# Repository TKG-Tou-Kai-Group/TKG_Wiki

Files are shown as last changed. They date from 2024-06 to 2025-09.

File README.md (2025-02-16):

# TKG Wiki

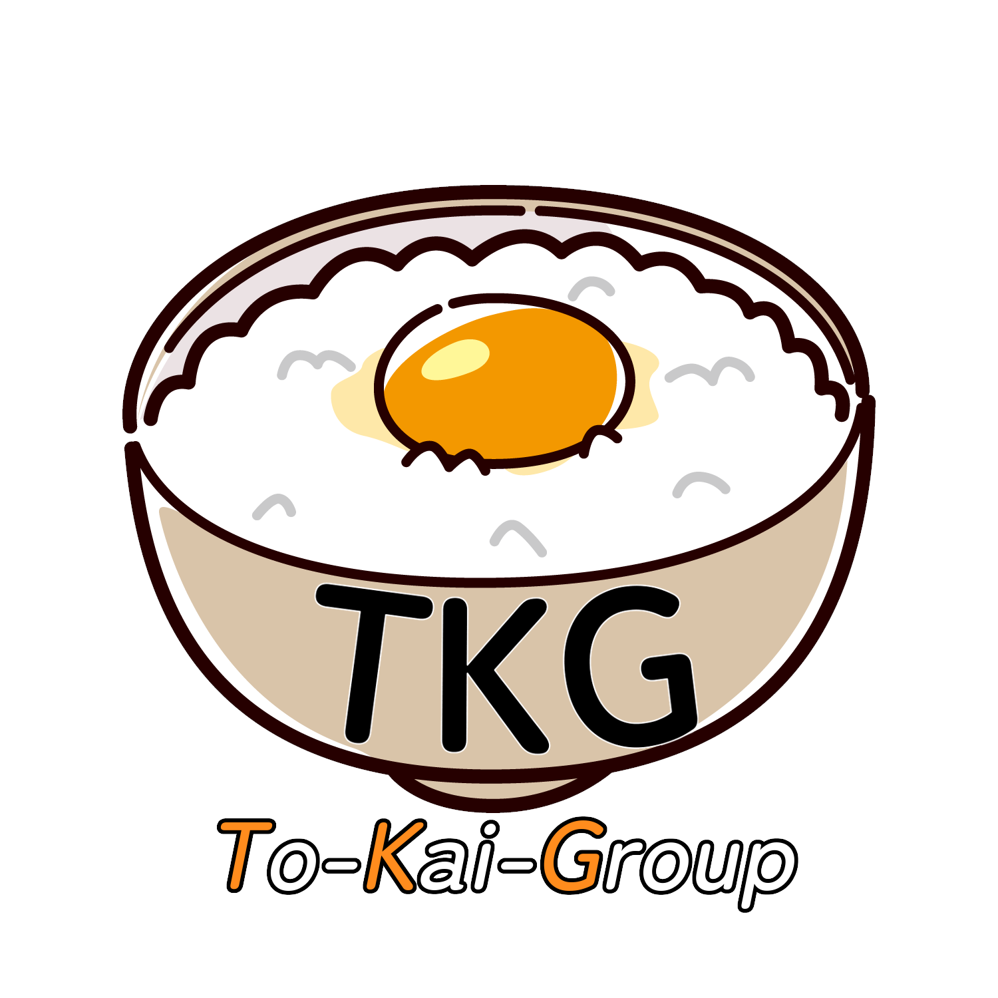
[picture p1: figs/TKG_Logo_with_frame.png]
ロゴ


## TKGについて

[CoRE](https://core.scramble-robot.org/)というエンジニア選手権に出場するために結成された東海地方4社の社会人連合チームです。メンバーにはお酒好きが多く、お酒がエネルギー源です。前回大会の目標は「技術賞・個人賞の受賞」でした。革新的技術賞を受賞できましたが、各構成要素の信頼性が低く同盟戦では活躍できませんでした。2024年度は「各構成要素の信頼性向上」により同盟戦で活躍できるロボットを開発することで、総合優勝を目指します！x（旧Twitter）上の#CoREJP_TKGで進捗状況や技術資料を公開中です。微力ながら大会を盛り上げていきますので、どうぞよろしくお願いします。

## 本Wikiの内容について

各出場年毎に作成した設計検討資料をアップロードしています。内容として、ウォーターフォール型開発モデルに基づく方針決定、外部設計、詳細設計の検討資料に加えて、作成したロボットの3DCADデータや回路基板データがあります。詳しい情報は各年毎のREADMEを参照してください。

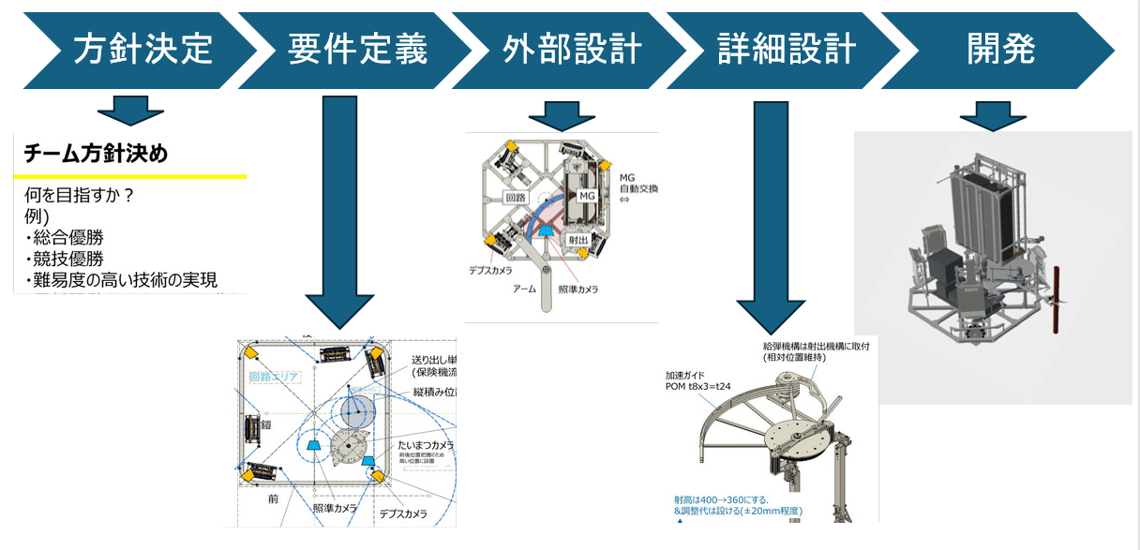
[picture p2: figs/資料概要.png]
資料概要


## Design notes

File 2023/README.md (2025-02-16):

# TKG - CoRE 2023 資料

CoRE 2023に出場した際に作成した企画・構想段階の資料や機能ブロック図などが格納されています。

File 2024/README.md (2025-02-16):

# TKG - CoRE 2024 資料

CoRE 2024に出場した際に作成した資料です。以下の4つのフォルダからなります。

- [本命マシン_開発資料](./本命マシン_開発資料)

  新規開発の機能を盛り込んだ機体の開発時に作成した方針決定、構想DR、外部仕様DR、詳細設計レビューやスケジュールの資料が格納されています。

- [保険マシン_開発資料](./保険マシン_開発資料/)

  昨年開発したマシンを元に確実に動作することを目標としたバックアップ用機体の構想設計、詳細設計の資料が格納されています。

- [02_詳細検討](./02_詳細検討/)

  具体的に設計したロボットの3DCADや基板データ、計算書などが格納されています。
  3DCADデータとして、比較的利用が容易なFusion 360用のアーカイブファイルと様々な3DCADで開くことができるSTEPファイルをZIP圧縮したものを用意しています。

- [提出済書類](./提出済書類/)

  大会運営に提出した審査資料が格納されています。大会運営が公開する以前から他のチームの参考として公開しているものとなります。
  大会運営から公開されている全チームの資料は[こちら](https://drive.google.com/drive/folders/1EVPRaTSho4vyFh4uzZCRXxRpLFyxL3u6)です。

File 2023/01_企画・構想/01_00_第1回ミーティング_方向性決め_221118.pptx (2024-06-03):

## 第1回 チームMTG

□方向性決め
□日程確認

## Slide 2

チームの目標設定

何を目指すか
例えば，
・総合優勝
・競技優勝
・難易度の高い技術の実装(勝敗を問わない)
・最低限動くものをみんなで作り上げること
・学生が絶対にできないことをやる(勝敗を問わない)
・社会人らしさを
設定した各目標に対して、それを実現するロボットはどんなものか考える．

最低限動くもの(一通りの競技ができる)を本年度の目標とする
回を重ねるごとに付加価値をつけていく(同じルールは3年間)

チーム目標

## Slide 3

日程

タイトです．

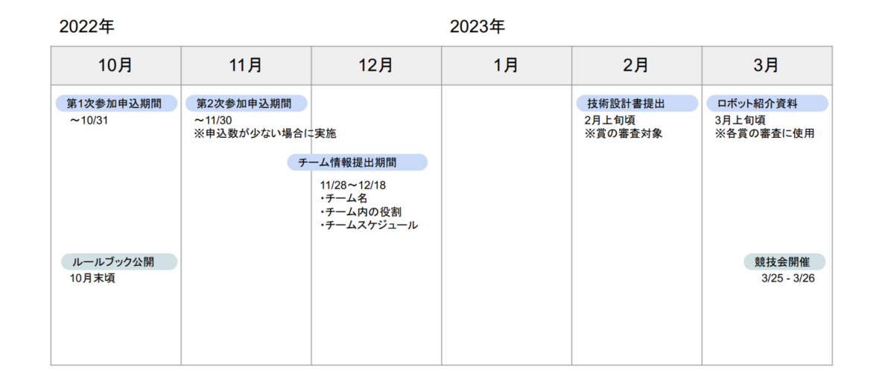
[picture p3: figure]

アイデア出し
方針決定
計画立案

構想
要件定義

12/M

現実的な予定

詳細検討

製造・手配

組立

検証・調整

1/M

2/M

理想的な予定

詳細検討

製造/組立/手配

正月休み明けから
製造に入るイメージ

検証・調整

脚周りは先行して製作・動作確認

独立要素の先行詳細検討
(足周りとか)

先行手配

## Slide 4

方向性決め

汎用型
└1台で一通りの競技をこなせる
└移動機能:対向2輪，オムニ3輪，オムニ4輪，メカナム(4輪)，独立4輪ステア
└投射機能:ローラー，ベルト，ばね・ゴム
└装填機能
└旗回収/設置機能
└たいまつ設置機能
汎用型+付加価値
操縦者補助
└
回転砲塔
転倒復帰

特化型
└例)固定砲台:攻撃に全振り

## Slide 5

最低限のアイデア

・対向2輪
・投射機構1発:ベルト式 or ローラー式
・仰角調整機構有り
・装填機構:自重落下
・操作画面はデフォルト
・旗/たいまつ回収/設置機構：つかむ+上下動(アクチュエータ2個)

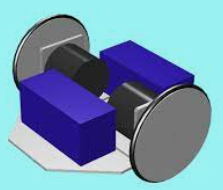
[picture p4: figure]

最低限＋αのアイデア

・全方向移動：オムニ3/4輪，メカナム
・

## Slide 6

ユニークなアイデア

・発射機構安定化：ジンバル
・多方向素早い攻撃：回転砲塔
・フリスビー迎撃
・操縦者補助：操作画面上の表示追加, 視界拡張
・防衛機構：鎧可動，自動回避
・目視外攻撃
・フリスビー回収機構

個人的な
操縦者に優しいロボット
⇒操作画面に工夫(飛ぶ位置表示)，投射遅延が小さい，自由自在に動ける

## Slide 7

設定した目標を達成するロボット

・全方向移動
・回転砲塔
・投射機構：縦投げ && 回転
・仰角調整:回転数制御でホイップさせる？（先行検討)
⇒仰角調整専用機構は付けたくない(アクチュエータ数、砲塔剛性)
・装填機構:？
・補給：マガジン式
⇒ネックになりそう。アイデア要検討
・操作画面はデフォルト
・旗/たいまつ回収/設置機構：つかむ+上下動(アクチュエータ2個)
→一旦無しで。後付けは可能

本年度目標

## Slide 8

日程

アイデア出し
方針決定
計画立案

構想
要件定義

12/M

現実的な予定

詳細検討

製造・手配

組立

検証・調整

1/M

2/M

理想的な予定

詳細検討

製造/組立/手配

正月休み明けから
製造に入るイメージ

検証・調整

独立要素の先行詳細検討
(足周りとか)

先行手配

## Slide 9

To Do

項目 | 内容 | 備考
進捗管理表作成 | | 要素に分解し， 担当者名も入れる
構成検討 | ロボットの搭載機能決定 | 例)回転砲塔タイプ 回転砲塔，移動機構，装填機構，旗立・たいまつ専用機構？
↓
機構検討 | 具体的な機構の決定
外部仕様 | H/W・S/W仕様明確化

本日会議で搭載機能は凡そ決定済．
まとめ&ポンチ絵を描く→To Do の明確化
→進捗管理表作成

ここまで
11/E

メカ，H/W，S/Wでの議論時は他担当も1人は入ること(オブザーバー的な役割)
(目的:進捗把握，情報共有，助言)
Discordのチャンネル上であれば相互に誰でも見れるので問題ないかと

メカ：伊藤，日高，田上，阿部，永松，大濱
H/W:佐藤，菊池，千代
S/W:佐藤，菊池，千代

?

永松さんはシステム仕様検討(S/W寄り)？

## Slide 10

現時点での懸念事項

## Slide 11

現時点での懸念事項

予算どれくらいか
一人どれくらい出しても良いでしょうか…？

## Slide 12

総大将決定戦

セッティング:3分
競技前半:1.5分
ハーフタイム:1分⇒フリスビー補給
競技後半:1.5分

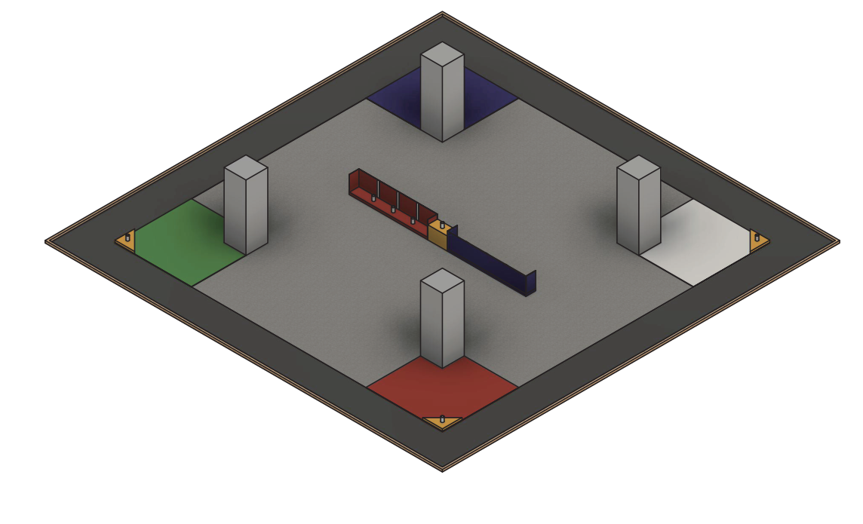
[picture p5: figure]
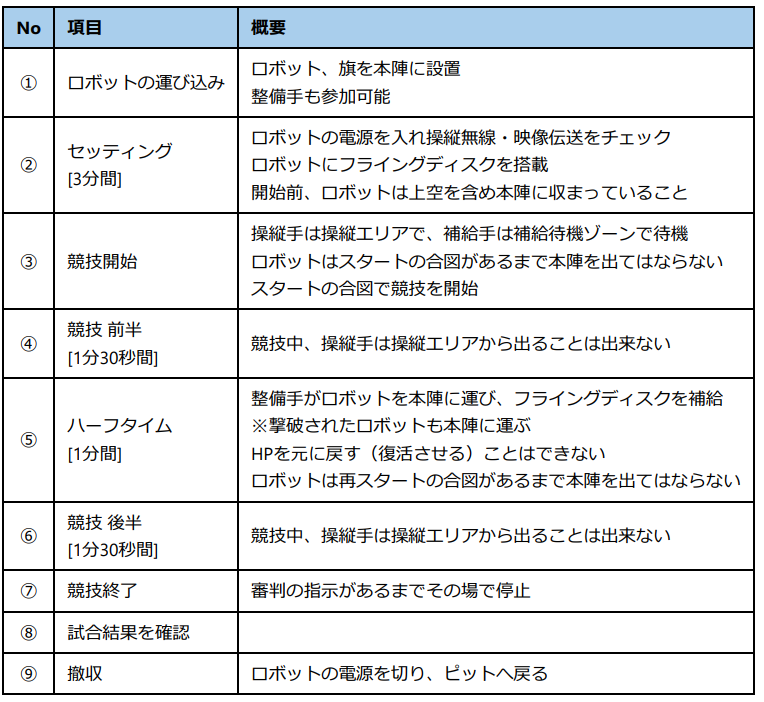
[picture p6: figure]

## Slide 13

決勝T

セッティング:3分
競技前半:5分
セッティング:3分
⇒フリスビー補給，作戦会議
競技後半:5分

補給ゾーン

Vスポット

旗置き場

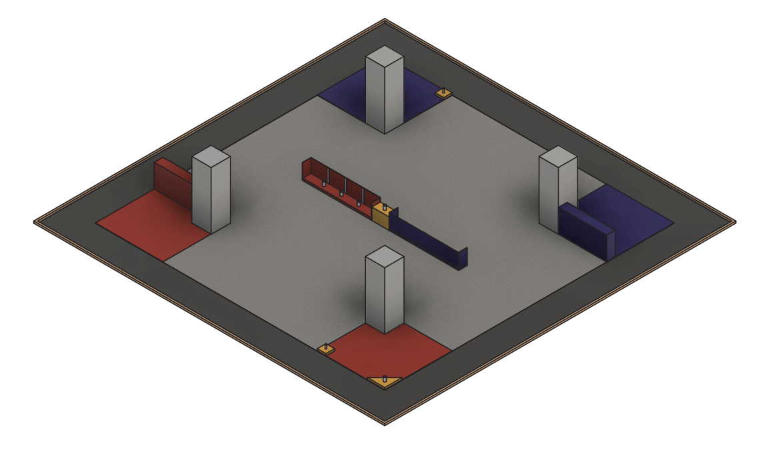
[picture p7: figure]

本陣

領地獲得スポット

たいまつ設置
→フリスビー補給権獲得

補給ゾーン

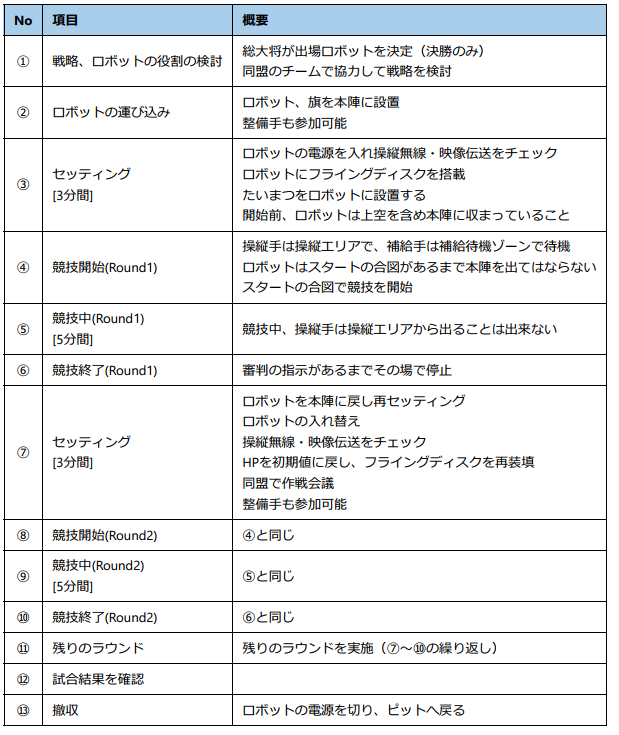
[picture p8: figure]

旗置き場

敵足軽1台撃破
→将軍ロボが旗保持権獲得
→将軍ロボが敵本陣Vスポットに旗設置→勝利

退避ゾーン

本陣

Vスポット

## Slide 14

雑メモ

・進め方，アイデア出しのアプローチ方法についてメモ

例)高専ロボコンでの進め方
ルール発表(4/E)→ルール読み合わせ→[GW中]アイデア出し(8チーム, ブレスト)
→[5/M]第一回アイデア選考会(4チームに絞る)
→要素検討→[5/E？]第二回アイデア選考会(正式に2チーム作成)→
構想検討(NHKに提出するアイデアシートも同時進行)→詳細検討
→[6月・7月]第一回試作→お披露目会→[8月中]第二回試作(本番機になるパターン多し)
→練習・調整→[9月？]お披露目会・大会準備(チェックシート作成等)・本番想定の練習・予備部品作成
→本番(地区大会：10月)→全国大会11月
社会人の場合工数不足なので下記のように短縮する
アイデア出し→方針決定→構想検討→詳細検討→試作→評価・改良→本番

2022.11.2 伊藤

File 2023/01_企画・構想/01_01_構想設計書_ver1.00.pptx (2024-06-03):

## 【Scramble CoRE】 構想設計書 チーム：TKG

全体承認済み

Ver1.01 佐藤

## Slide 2

日程概要

DR1
(構想設計 審査)

DR2
(外部仕様 審査)

DR3
(詳細設計 審査)

DR4
(評価結果 審査)


アイデア出し
方針決定
計画立案

全体設計

詳細設計

製造※1・手配

組立

検証・調整

12/M

1/F

2/M

先行手配

[審査対象]
DR1:どんな機能を盛り込むか？全体構成は？
スケジュール/分担
DR2:どのような機構/構成で実現するか？
機能間のインターフェース
DR3:製造上の課題はないか？
DR4:修正が必要な点はないか？

※1 正月休み明けから製造に入るイメージ

11月Eまでの宿題
・進捗管理表の作成
・構想設計　仕様書
(=足回り、投射機構、装填機構、
制御構成への要求定義書類)
・ホイップ機構試験機 設計
※3Dプリンタ+アルミフレームで簡単に作れること

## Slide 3

チーム目的
「一通りの競技ができること」
目標
・1台で一通りの競技をこなせること(汎用型)
・最低限動くものを完成させる
・育成により付加価値をつけていく
　※3年間は同じルール

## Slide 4

機能構成
・全方向移動:オムニ4輪
・回転砲塔
・投射機構：縦投げ && 回転
・仰角調整:回転数制御でホイップさせる？（先行検討)
⇒仰角調整専用機構は付けたくない
　　　(アクチュエータ数、砲塔剛性)
・装填機構:
・補給：マガジン式
・操作画面~~はデフォルト⇒~~に情報をオーバーレイ
　(ルールメイキングとして、無線系統の削減が必要になりそうなため)
・旗/たいまつ回収/設置機構：つかむ+上下動(アクチュエータ2個) →一旦無しで。後付けは可能

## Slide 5

担当表

対象 | 主担当
全体構成 | 伊藤(万)
車体(足周り+フレーム) | 田上
足回り | 田上
投射機構 | 阿部
回転砲塔 | 日高
装填機構 | 日高
マガジン機構 | 日高
電装系統 | 佐藤
非常停止機能 | 千代
統括制御系 | 菊池
UI系 | 永松
射出制御系 | 佐藤
走行制御系 | 佐藤

※各自の業務負荷(Scramble Coreまたは本業)に応じて適宜負荷調整する

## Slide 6

承認

氏名 | 承認(○) | コメント
例)鈴木 | ○ | 海外調達品(中国)の納期は要注意して進めること
伊藤 | ○ | 担当間のコミュニケーションを十分取り、後戻り業務を最小限にして 進めましょう。
佐藤 | 〇 | 無理せず楽しましょう
日高 | ○ | 情報追うの遅くてすみません。見たらbボタン押すようにします。
菊池 | ○ | 遅くてすみません！がんばります！
阿部 | 〇 | 発射機構は試作機→本番機の変更を最小限に抑える
千代 | 〇 | とくになし
永松 | 〇 | 役立てる様頑張ります．そして楽しむ．
大濱 | 〇 | 皆さんのサポートができるよう努力します．
田上 | 〇 | 設計&製造面でサポートします。
寺部

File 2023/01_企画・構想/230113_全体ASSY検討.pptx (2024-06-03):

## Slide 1

タスク表・フォロー表

"G:\マイドライブ\Scramble-CoRE\01_企画・構想\230114_DR3メモ.xlsx"

旋回砲塔質問事項
https://docs.google.com/presentation/d/1yQDwXKtcUiF0FoB08fJTNh-uwBbIvaBs8e14fGZGu7Y/edit?usp=sharing

重量管理表
"G:\マイドライブ\Scramble-CoRE\02_詳細検討\重量管理表_2023.xlsx“
https://docs.google.com/spreadsheets/d/1AEPZGchSj93YvSv4dRJGASU1HNefhxek/edit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

//メモ
・どなたか議事録を
・菊池さん ~16:00まで
└進捗・相談事項あれば先に聞く/関係するメカ(全体ASSY)先に説明

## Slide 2

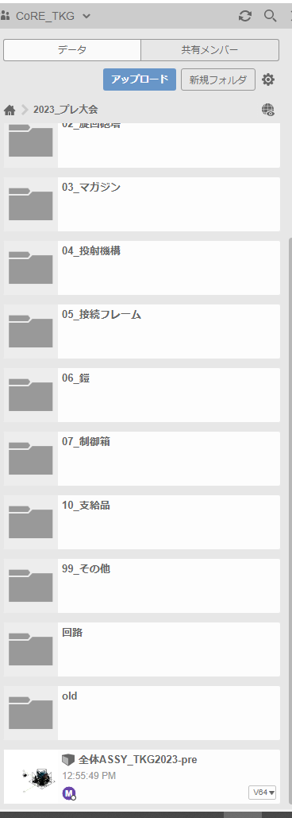
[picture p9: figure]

どなたか議事録を

全体ASSY検討

伊藤(万)

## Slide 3

全体ASSY検討

審議したい内容;
・各要素のレイアウトはこれで良いか？
└MG配置
└鎧配置
└制御箱
└HPインジケータ

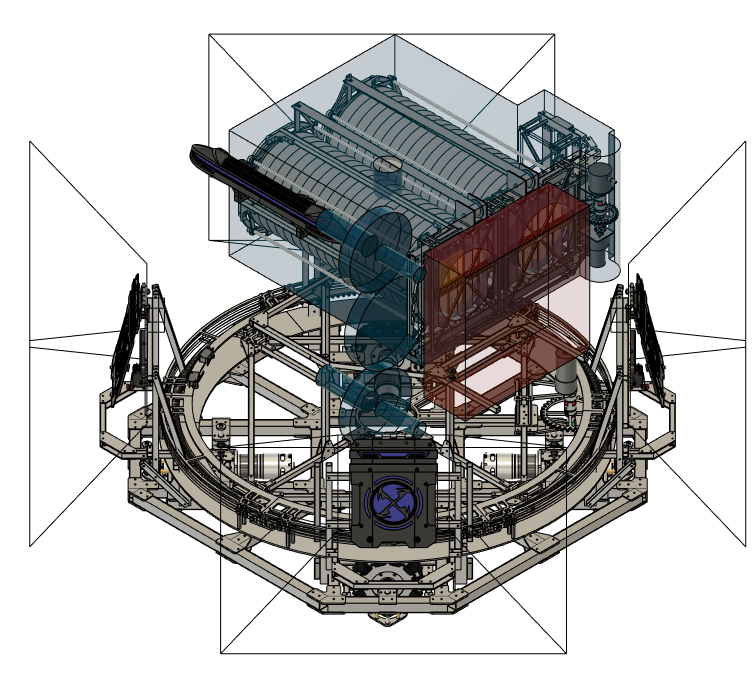
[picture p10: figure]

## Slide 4

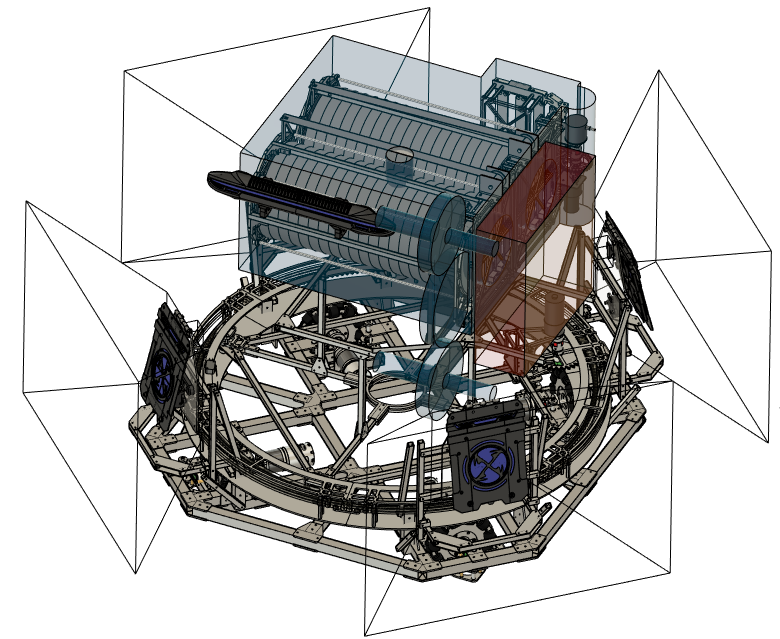
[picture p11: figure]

カメラ設置エリア
・接続フレームに固定

接続フレーム
旋回機構と上部機構・回路をつなぐ

HPインジケータ
・前面&カメラより上に設置
・接続フレームからフレーム伸ばして固定

制御箱
・MG横に配置
・基板縦置き
・100x300x300

鎧
・最外殻に配置
・最低限のバンパー取付

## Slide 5

全体ASSY検討

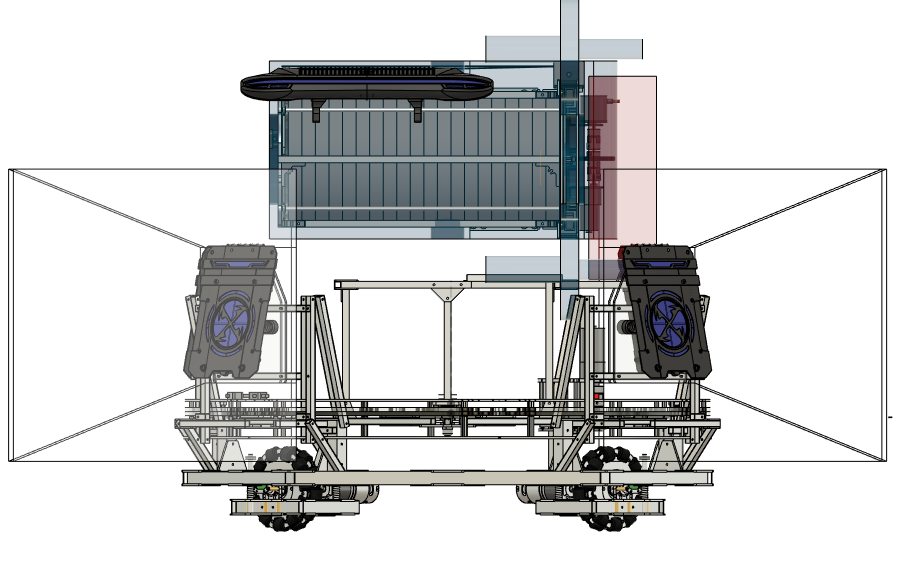
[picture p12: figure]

HPインジケータ

制御箱

接続フレーム

1/15時点未完事項
・接続フレームとMGとの接続
・旋回機構と足周りフレームの接続
・旋回部の配線取り回し
・HPインジケータ，制御箱との接続

前

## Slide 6

全体ASSY検討

フレーム接続図

投射機構

相対関係維持のため投射機構はMGに固定する
(接続フレームとは繋がない．繋いでも補強材程度)

マガジン

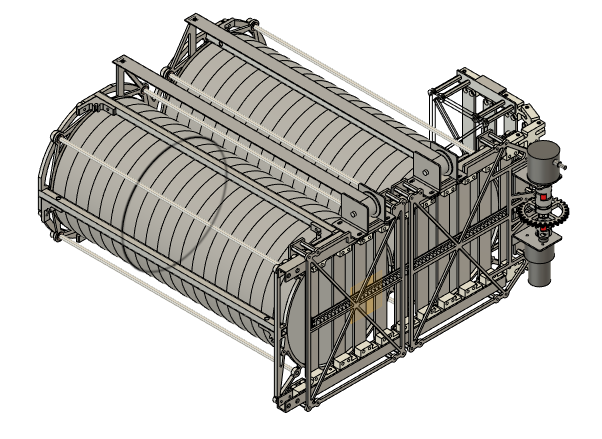
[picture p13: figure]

分離時

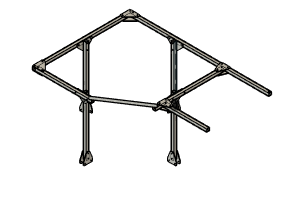
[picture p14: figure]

接続フレーム

制御箱

カメラユニット

旋回機構

HPインジケータ

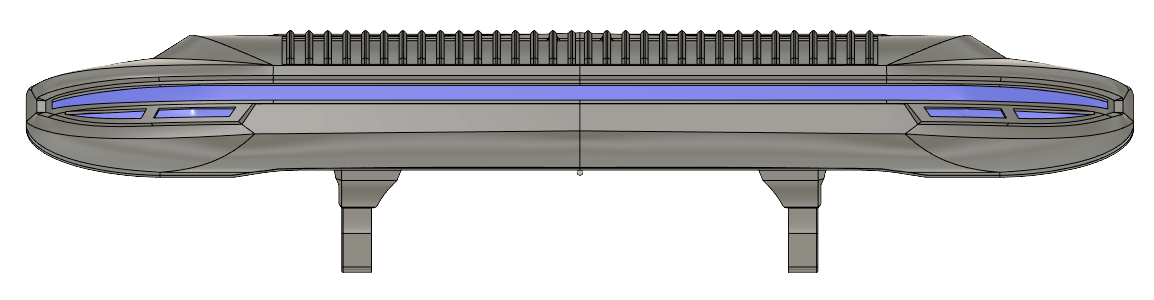
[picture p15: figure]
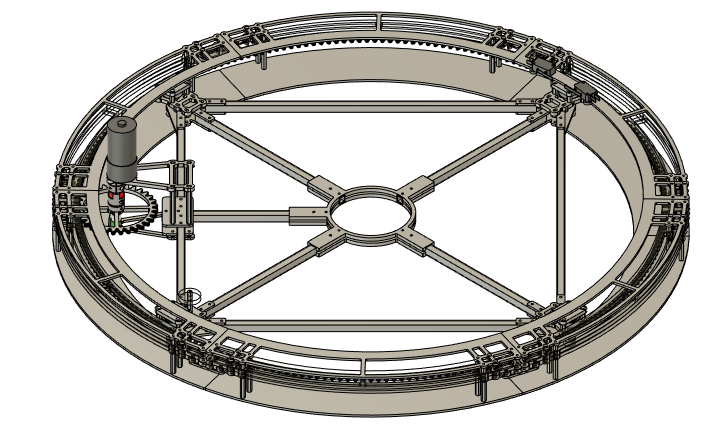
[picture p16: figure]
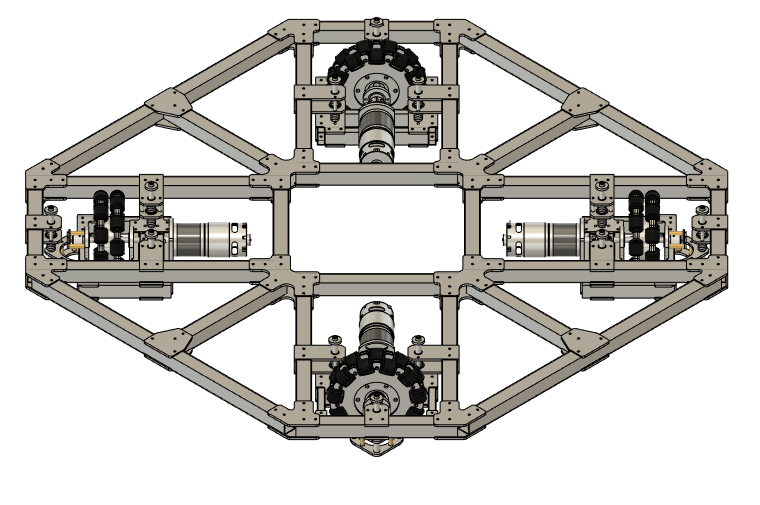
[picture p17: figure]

足周りフレーム

足ユニット

鎧

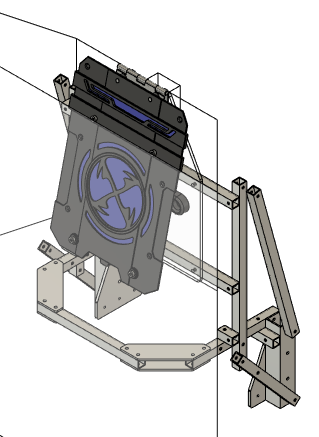
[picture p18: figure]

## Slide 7

全体ASSY検討

MG/投射機構レイアウト

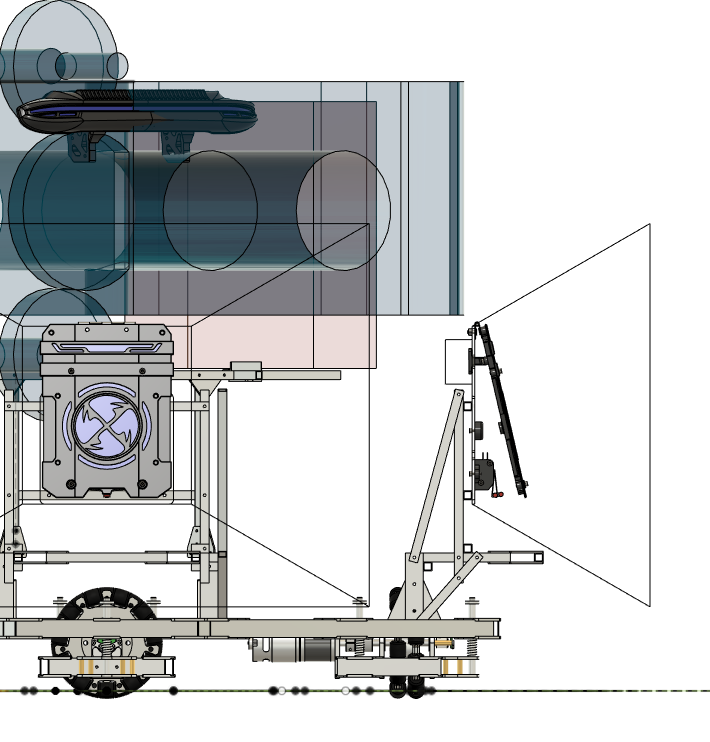
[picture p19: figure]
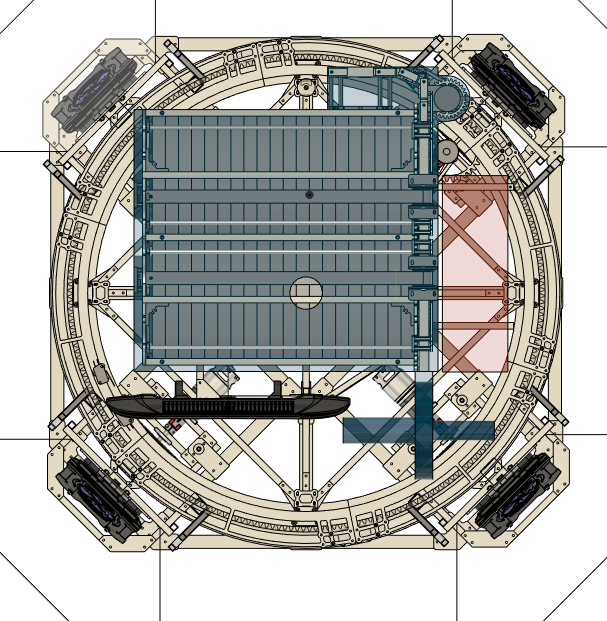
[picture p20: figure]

水色:投射機構の最大動作円
→鎧に干渉しないギリギリで配置(10mm程度)
赤色:MGの最大動作円
→鎧の侵入不可領域を侵犯しないギリギリ(10mm程度)

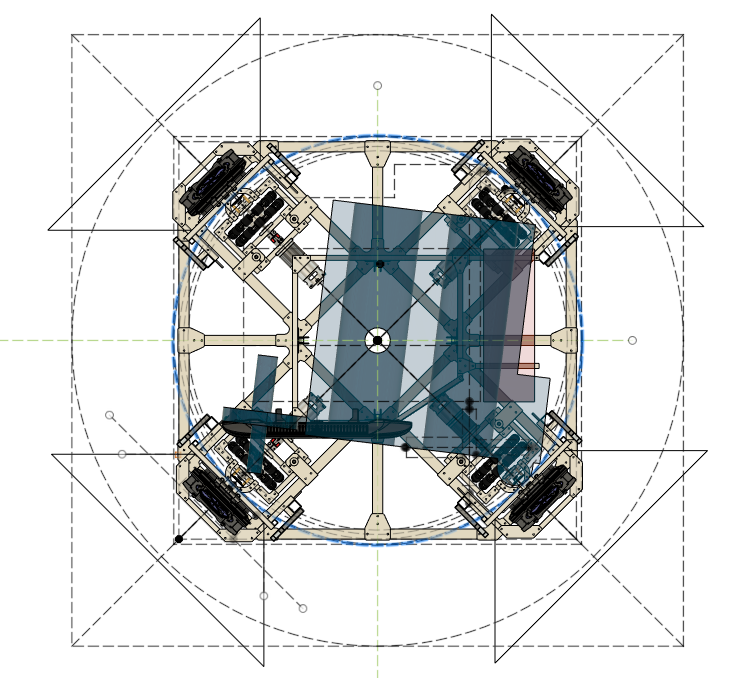
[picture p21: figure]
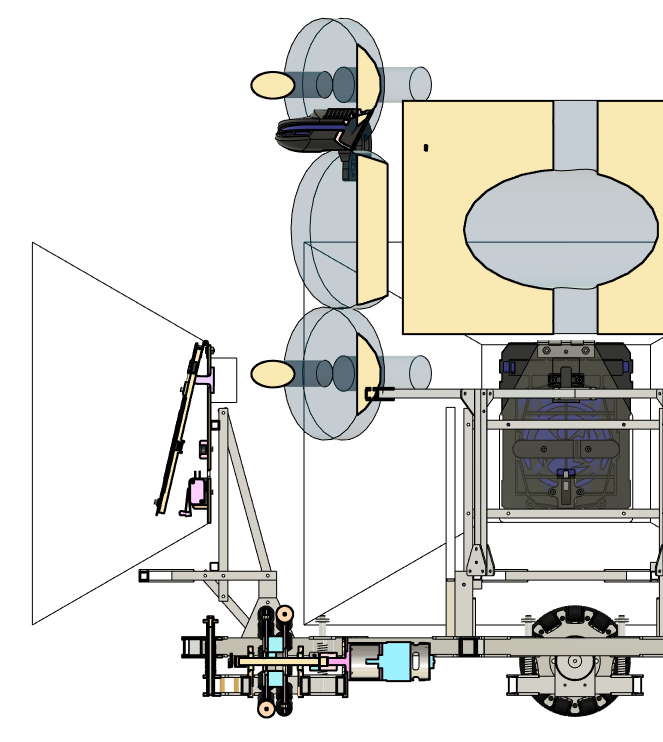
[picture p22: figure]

上

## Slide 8

全体ASSY検討

鎧

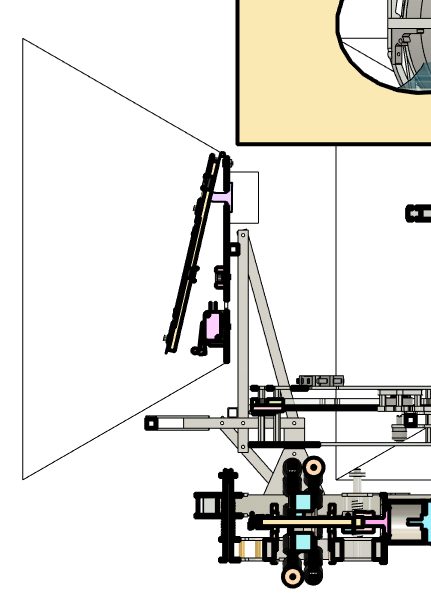
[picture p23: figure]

最低限のバンパー
・柱のようなものは防護できるが、突起物は防げない

A

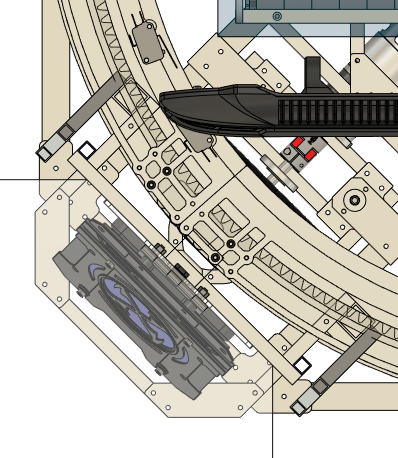
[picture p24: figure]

A

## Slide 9

全体ASSY検討

鎧

鎧ユニットごと外す場合はこの角材から

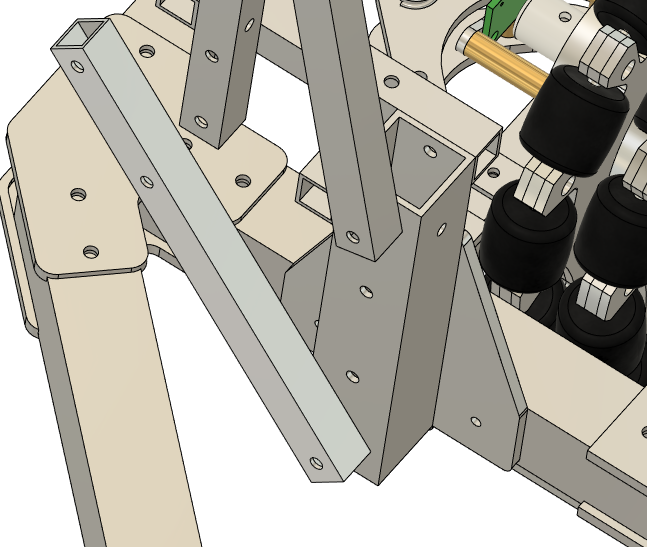
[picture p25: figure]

足フレーム組むときに先につけておく
(以降、外さない)

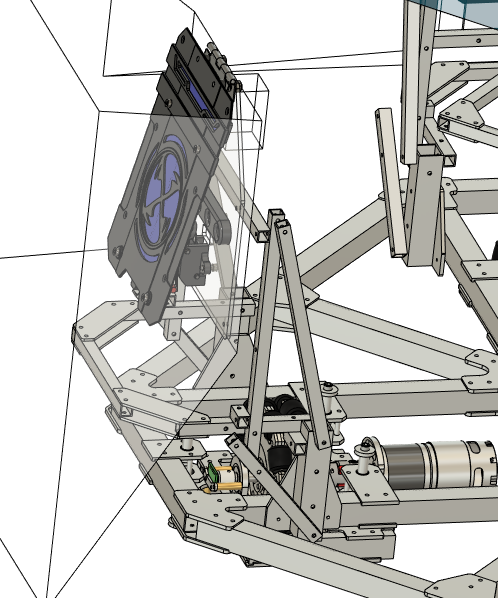
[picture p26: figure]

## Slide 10

全体ASSY検討

旋回部配線取り回し

"G:\マイドライブ\Scramble-CoRE\02_詳細検討\02.旋回砲塔\旋回部配線検討\こんなイメージ.mp4"

・同軸2円筒に挟まれた空間に配線を通す
・内側円筒に巻き付くイメージ
・ばらけ防止のため編組スリーブに入れる．
動作反転時に屈曲が厳しくなるようであればソフトナイロンチューブを配線束に入れて
硬くする．
・摺動面は樹脂シート(ダイソー)を貼る && グリス塗布　により摺動性確保

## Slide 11

・重量配分のお話
・製作のお話
└優先度設定
└
└加工割り振り

"G:\マイドライブ\Scramble-CoRE\01_企画・構想\230114_DR3メモ.xlsx"

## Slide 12

ポケット

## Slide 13

全体ASSY検討


鎧を安全位置まで引っ込めると、上部機構が鎧の侵入不可領域に干渉
⇒鎧の防護は諦める(最低限、フレームより引っ込める)
展開式の防護機構という手も有あり．

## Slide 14

全体ASSY検討

鎧


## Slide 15

"G:\マイドライブ\Scramble-CoRE\00_概要\autoreferee_manual.pdf"


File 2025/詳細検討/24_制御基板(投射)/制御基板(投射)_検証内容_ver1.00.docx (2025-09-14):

・ホイール回転用のMDへの制御信号は４ピン指定でしたが、過去の基板を見ると3ピンでしたのでそちらに合わせています。
→すみません。3ピンの間違いでした。

・MGセンサ、PWON出力のピン配置を去年と同じにしています、変更必要なら変えます。

→PWONは去年と同じ配置のつもりでしたが、どこかの資料間違っていましたでしょうか？MGセンサはその先の基板も作っていただくのでどちらでも大丈夫です。

・RS232の変換ICに5VレベルのPICの信号を入れています。動作する記事はあったのですが、必要なら5V対応の変換ICに変更します。

→データシートざっと見た限りは仕様上OKだと思います。不安なら、多少コストかさんでも5V対応品にしていただいてもかまいません。

・PICでシリアル通信のチャンネルが2chで、1chがコントローラ、もう1chがエンコーダの割り込み入力と被っている為、他UIとのシリアル通信はジャンパーピンで選択制にしており、同時使用は不可能です。

→他UIとのシリアル通信はTXだけの利用でも難しいですか？(残弾数情報は制御基板(投射)からしか送れないため)


Q.データシートの標準測定回路を見ると、入力側も電解コンデンサが使用されているが、積層セラミック？でよいか？


Q.未使用の入力端子(3,4A,B)はGND接続ではなく、オープンでよい？


・Detect(検出)では？Distanceだと距離だと思います（私も英語よわよわなので間違ってるかも）


Q.ソレノイド駆動用FETは別基板？


Q.VIO側のパスコンは不要ですか？


・OPRON信号については、上記コネクタ配置と分圧抵抗の実装をお願いできますか？
（公式の基板仕様が現時点不明確なのでなるべく対応できるようにしておきたい）

※(佐藤メモ、生田さんには関係ないです)
公式基板がオープンコレクタ出力の場合、投射基板で5Vプルアップ、走行基板は分圧のみ実施して5V,3.3Vの共用利用する。分圧抵抗、プルアップ抵抗の合成抵抗に注意（設計計算のこと）


Q.非常停止信号は、3.3Vプルアップでは難しいですか？NGなら走行制御基板で分圧します。

・走行制御基板(3.3V)にも並列して非常停止スイッチ繋ぐため、プルアップは原則片方だけ実装することになると考えています。

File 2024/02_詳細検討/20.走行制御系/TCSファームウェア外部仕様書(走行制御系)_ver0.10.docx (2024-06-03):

TCSファームウェア

外部仕様書

(走行制御系)

※TCS:TKG Control System

版数：Ver0.10

作成：TKG 佐藤

# 1. 処理設計

## 背景・目的

CoREに参加するためのロボットにおいて、走行制御にかかわる制御機能を提供する。

## システム機能要件一覧

システムの機能要件について、一覧で記載する。

### 走行機能(Must)


対象 ：足機構

機能概要 ：

・指令値(機体並進速度、角速度)を基に足モータをサーボ制御する。

現調項目 ：

・モータ回転方向
モータ出力軸から見てCW方向への回転を正方向とする。モータドライバに正の指令電圧を与えた場合に正方向に回転するよう配線する。

・モータ配置

### 状態表示機能(Must)

対象 ：全体

概要 ：

・機体状態をLCDディスプレイに表示する。表示内容は、以下の通りとする。
‣バッテリ電圧
‣アラームメッセージ

・LED(赤、青)によって、現在の状態を示す。

## 状態遷移


システム全体の状態遷移は下図の通りである。

# 2. システム方式設計

## ハードウェア構成図

TCBの詳細仕様はKiCadプロジェクト参照のこと。

## ソフトウェア構成図

現行バージョンでは単一システムで構成するため、省略。

# 3. アプリケーション機能設計

## 画面設計

画面一覧を以下に示す。

全画面共通で、1行目(LCD黄色文字列)には、発生中の最新のアラームを示す。

### 画面名：非常停止

説明

・“非常停止状態”におけるLCD画面。

・表示内容はバッテリ電圧。

### 画面名：サーボオン

説明

・“サーボオン状態”におけるLCD画面。

・表示内容は、バッテリ電圧([%]を表示)/モータ温度(R,L)

### 画面名：アラーム

説明

・“アラーム状態”におけるLCD画面

・表示内容は、バッテリ電圧/アラーム

# 4. 外部インターフェース設計

## 外部インターフェース一覧

外部システムとの界面(インターフェース)の一覧を記載する。

### インターフェース名 ：ESTOP

方向 ：In

相手先システム名 ：非常停止ボタン

接続方式 ：B接点または、Nchオープンドレイン

### インターフェース名 ：OPRON

方向 ：In

相手先システム名 ：電源スイッチ、鎧仕システムの撃破判定出力

接続方式 ：B接点または、Nchオープンドレイン

### インターフェース名 ：PWON

方向 ：Out

相手先システム名 ：電源制御基板

接続方式 ：B接点または、Nchオープンドレイン

### インターフェース名 ：状態表示LED(赤、黄、緑)

方向 ：Out

相手先システム名 ：LED

接続方式 ：CMOS出力


### インターフェース名 ：SBUS

方向 ：In

相手先システム名 ：TPro

通信タイミング ：12.5msec周期

接続方式 ：

‣シリアル通信(負論理)

‣データ長 8bit, 偶数パリティ, ストップビット2bit, LSBファースト

‣ビットレート 100000bps

### インターフェース名 ：H-Link(High layer Link)

方向 ：In/Out

相手先システム名 ：統括制御系

通信タイミング ：送信は○○msec周期、受信は相手先システムに依存(12.5msec周期)

接続方式 ：RS232C

プロトコル ：Tinnycomm

### インターフェース名 ：L-Link(Low layer Link) (want)

方向 ：In/Out

相手先システム名 ：射出制御系

通信タイミング ：送受信は20msec周期

接続方式 ：RS232C

プロトコル ：Tinnycomm

### インターフェース名 ：LCDディスプレイ

相手先システム名 ：SSD1306

通信タイミング ：任意

接続方式 ：

‣I2C通信(I2C標準フォーマット)

‣ビットレート 100kbps

### インターフェース名 ：オムニホイール取付エンコーダ

相手先システム名 ：AS5601

接続方式 ：A,B相式(500pulse/rを4逓倍)

### インターフェース名 ：IMU

相手先システム名 ：MPU6050

通信タイミング ：10msec周期

接続方式 ：

‣SPI通信

‣4線式マスタモード,バッファサイズ64ビット,パリティビットなし

‣ビットレート 1000kbps


‣その他仕様は以下の通り。


### インターフェース名 ：バッテリ電圧

相手先システム名 ：バッテリ(LiFe 9.9V)

読み取りタイミング ：AD変換周期に依存

接続方式 ：ADコンバータ

### インターフェース名 ：モータ電流

相手先システム名 ：モータ電流(4個)

読み取りタイミング ：AD変換周期に依存

接続方式 ：ADコンバータ

### インターフェース名 ：MD出力

相手先システム名 ：Cytron SmartDriveDuo-60

指令タイミング ：5kHz

接続方式 ：PWM(5kHz)

## S-Linkインターフェース

S-Linkインターフェースは、外部仕様書に省略する。

## アラーム一覧

本ファームウェアにおけるアラームは以下のとおりである。アラームA~Cはアラーム状態が解除されるまで、本機の動作を停止する。

種別 (A~D) | 番号 | メッセージ | アラーム検出条件
A | 1 | バッテリ電圧低下 | バッテリ電圧が19.2[V]以下を1sec以上継続した(1セル3.2V以下)。
A | 2 | バッテリ電圧過大 | バッテリ電圧が26.4[V]以上を検出した(1cell4.4V以上)。
A | 3 | 足機構(FR)故障 | 足機構のモータ軸ロック保護機能によりロックを検出した。 (指令値と検出値との差異が〇〇m/sec以上の時間が1sec以上経過した)
A | 4 | 足機構(FL)故障
A | 5 | 足機構(RR)故障
A | 6 | 足機構(RL)故障
D | 1~4 | モータ過電流 (足機構FR~RL) | モータ過電流を検出した

# 5. 非機能要件設計

## 性能設計

・操縦に違和感なきこと。

・動作中にだんまり停止しないこと。

# 6. テスト方針

## 単体テスト(MT, UT)

☐全入出力IOが仕様通りに動作すること

## 結合テスト(IT)

☐現状なし

## システムテスト(ST)

☐FUTABA T10Jからラジコン操作が可能なこと

# 7. 参考資料

状態遷移の実装方法

[1] https://monoist.itmedia.co.jp/mn/articles/1211/07/news003_3.html


[2]アウトラインとか見出しの設定

http://office-qa.com/Word/wd560.htm

[3]外仕のテンプレ例

https://ittechnicalmemos.blogspot.com/2020/05/blog-post_21.html

[4]内仕の書き方

https://www.softech.co.jp/mm_191106_tr.htm

[5]LPFの作り方

https://qiita.com/motorcontrolman/items/39d4abc6c4862817e646

TCS ファームウェア外部仕様書(走行制御系)

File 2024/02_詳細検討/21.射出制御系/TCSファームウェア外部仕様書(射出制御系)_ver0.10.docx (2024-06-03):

TCSファームウェア

外部仕様書

(射出制御系)

※TCS:TKG Control System

版数：Ver0.10

作成：TKG 佐藤

# 1. 処理設計

## 背景・目的

CoREに参加するためのロボットにおいて、射出制御にかかわる制御機能を提供する。

具体的には、投射機構、装填機構、旋回機構の制御を実現する。

## システム機能要件一覧

システムの機能要件について、一覧で記載する。

### 投射機能(Must)

対象 ：投射機構

機能概要 ：

・指令値(目標までの距離、目標の高さ)にフライングディスクを投射するようローラ回転数指令を生成し、ローラ回転数を制御する。

アラーム検出条件 ：

・ホイール回転数と指令値との差異が閾値以上の時間が1sec以上経過した時点で、ローラの故障とし、アラームAとする。

現調事項 ：

・TBD

### 装填機能(Must)


対象 ：装填機構

機能概要 ：

・装填機構を制御する。
※装填間隔1sec以内

アラーム検出条件 ：

・位置指令値と位置検出値の差異が閾値以上の時間が1sec以上経過した時点で、シャッター機構の故障とし、アラームAとする。

・リミットスイッチがリミットを検出した時点で、アラームDとする。
アラームD発生後、低速送り動作によって適正位置への移動をリトライ

現調事項 ：

・リミットスイッチ位置

・各シャッター位置

### 旋回機能(Must)

対象 ：旋回機構

機能概要 ：

・指令値(目標角度)に砲塔を制御する。

アラーム検出条件 ：

・位置指令値と位置検出値の差異が閾値以上の時間が1sec以上経過した時点で、旋回機構の故障とし、アラームAとする。

・リミットスイッチがリミットを検出した時点で、アラームDとする。
アラームD発生後、低速送り動作によって適正位置への移動をリトライ

現調事項 ：

・リミットスイッチ位置

・TBD

### 状態表示機能(Must)

対象 ：全体

概要 ：

・機体状態をLCDディスプレイに表示する。表示内容は、以下の通りとする。
‣バッテリ電圧
‣アラームメッセージ

・LED(赤、青)によって、現在の状態を示す。

## 状態遷移


システム全体の状態遷移は下図の通りである。

※サーボオン状態でのアラームD時は、青点灯＋赤の点滅とすること

# 2. システム方式設計

## ハードウェア構成図

TCBの詳細仕様はKiCadプロジェクト参照のこと。

## ソフトウェア構成図

現行バージョンでは単一システムで構成するため、省略。

# 3. アプリケーション機能設計

## 画面設計

画面一覧を以下に示す。

全画面共通で、1行目(LCD黄色文字列)には、発生中の最新のアラームを示す。

### 画面名：非常停止

説明

・“非常停止状態”におけるLCD画面。

・表示内容はバッテリ電圧。

### 画面名：サーボオン

説明

・“サーボオン状態”におけるLCD画面。

・表示内容は、バッテリ電圧([%]を表示)/モータ温度(R,L)

### 画面名：アラーム

説明

・“アラーム状態”におけるLCD画面

・表示内容は、バッテリ電圧/モータ温度(R,L)/アラーム

# 4. 外部インターフェース設計

## 外部インターフェース一覧

外部システムとの界面(インターフェース)の一覧を記載する。

### インターフェース名 ：S-Link

相手先システム名 ：統括制御系

通信タイミング ：送信は○○msec周期、受信は相手先システムに依存(12.5msec周期)

接続方式 ：

‣シリアル通信

‣データ長 8bit, 偶数パリティ, ストップビット2bit, LSBファースト

‣ビットレート 115200bps

### インターフェース名 ：SBUS


相手先システム名 ：FUTABA R3001SB

通信タイミング ：相手先システムに依存する(12.5msec周期)

接続方式 ：

‣シリアル通信(負論理)

‣データ長 8bit, 偶数パリティ, ストップビット2bit, LSBファースト

‣ビットレート 100000bps

### インターフェース名 ：LCDディスプレイ

相手先システム名 ：SSD1306

通信タイミング ：任意

接続方式 ：

‣I2C通信(I2C標準フォーマット)

‣ビットレート 100kbps

### インターフェース名 ：エンコーダ

相手先システム名 ：省略

通信タイミング ：省略

接続方式 ：

AS5048Aに関しては、下記の通り。その他2相式エンコーダは省略

‣SPI通信(LTC6820を経由)

‣4線式マスタモード,バッファサイズ64ビット,パリティビットなし

‣ビットレート 100kbps


‣その他仕様は以下の通り。

### インターフェース名 ：IMU

相手先システム名 ：MPU6050

通信タイミング ：〇〇msec周期(ファームウェア側マスタのため任意タイミングで利用可)

接続方式 ：

‣SPI通信

‣4線式マスタモード,バッファサイズ64ビット,パリティビットなし

‣ビットレート 1000kbps


‣その他仕様は以下の通り。

### インターフェース名 ：バッテリ電圧

相手先システム名 ：バッテリ(LiFe 9.9V)

通信タイミング ：任意

接続方式 ：

‣ADコンバータ

### インターフェース名 ：MD出力

相手先システム名 ：省略

通信タイミング ：PWM20kHz,MC402CR:12.5ms周期

接続方式 ：

‣PWM方式。詳細は、MC402CR(双葉電子産業)説明書を参照のこと。

## S-Linkインターフェース

S-Linkインターフェースは、外部仕様書に省略する。

## アラーム一覧

本ファームウェアにおけるアラームは以下のとおりである。アラームA~Cはアラーム状態が解除されるまで、本機の動作を停止する。

種別 (A~D) | 番号 | メッセージ | 内容
A | 1 | バッテリ電圧低下 | バッテリ電圧が〇〇[V]or[%]以下を10sec以上継続した。
A | 2 | バッテリ電圧過大 | バッテリ電圧が△△[V]以上を検出した。
A | 3 | 機械故障(投射機構) | 右脚用モータでモータ軸ロック保護機能によりロックを検出した。
A | 4 | 機械故障(マガジン機構) | 左脚用モータでモータ軸ロック保護機能によりロックを検出した。
A | 5 | 機械故障(旋回機構) | アーム用モータでモータ軸ロック保護機能によりロックを検出した。
D | 1 | ソフトリミットオーバー (マガジン機構) | ソフトリミット範囲外の状態が60msec継続した。
D | 2 | ソフトリミットオーバー (旋回機構) | ソフトリミット範囲外の状態が60msec継続した。

# 5. 非機能要件設計

## 性能設計

・操縦時に違和感なきこと。

・動作中にだんまり停止しないこと。

# 6. テスト方針

## 単体テスト(MT, UT)

☐

## 結合テスト(IT)

☐現状なし

## システムテスト(ST)

☐

# 7. 参考資料

状態遷移の実装方法

[1] https://monoist.itmedia.co.jp/mn/articles/1211/07/news003_3.html


[2]アウトラインとか見出しの設定

http://office-qa.com/Word/wd560.htm

[3]外仕のテンプレ例

https://ittechnicalmemos.blogspot.com/2020/05/blog-post_21.html

[4]内仕の書き方

https://www.softech.co.jp/mm_191106_tr.htm

[5]LPFの作り方

https://qiita.com/motorcontrolman/items/39d4abc6c4862817e646

[6] MC402CR取扱説明書.pdf

TCS ファームウェア外部仕様書(射出制御系)

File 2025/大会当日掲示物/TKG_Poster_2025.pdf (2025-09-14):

# TKGロボット紹介


### バフ付与も可能な遠距離狙撃型アタッカーと、


### 精密狙撃が可能なオートタレットにより同盟戦で活躍します！

## チーム紹介

### 東海地方を中心とした社会人チームです(4社連合)。 ロボコン経験の有無に関わらずロボット開発を楽しむことがモットーです。 初顔合わせのメンバーが多いですが、飲み会、合宿、人生のお悩み相談会 などで交友を深めており、チームメンバー間の仲が非常に良いです。

### 加入希望や質問はメールアドレスまで→

概要

## ロボットの特徴

### CoRE2025では同盟戦で主力となって活躍するべく、既存アタッカーの改良 およびオートタレットの新規開発を行いました。

<アタッカー> | <オートタレット>

高い命中精度
静止摩擦を考慮したLQR制御による
砲塔の高精度位置決めが可能。
遠距離でも正確に撃ち抜く。

確実な鎧検出
LED色のみに着目したテンプレート
マッチングによる安定した鎧検知。
近付いた相手機体を逃さず検知。

短時間で強化素材を回収/設置
操作によってずれても回収・設置ができる
受動的揺動構造を設けたハンド。
味方同盟にバフをかけて支援する。

長射程･射角調整機能
スナイパー的な運用が得意。
また、射角調整機構により本陣上部も攻撃可能。

全周視野による高い防御力
2台の360°カメラを使用した2Dアラウンドビュー。 周囲の状況を把握し、特に死角からの攻撃回避に有効。
防御力を高めることで自機(&同盟)のHP減少を抑制する。 また、操縦ブースにて総大将が状況を把握することに利用可能。

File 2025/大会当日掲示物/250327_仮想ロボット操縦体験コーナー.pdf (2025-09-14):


# バーチャルロボット操縦体験

## - 試合時間は1分間 - 相手のダメージパネルにディスクを当てて HPを多く減らした方の勝ち

# CoREのロボットを遠隔操縦してみよう！

## ルール

ディスクは20枚


ダメージパネルはこれ | 選手と同じ環境で対戦できる！


操縦画面も
選手と同じ一人称視点！

ロボットHP 残り時間

# 操作方法

## 俯瞰画像


表示

## ディスク

発射

## 前後左右

移動

旋回

## 同時押し

で

## リセット

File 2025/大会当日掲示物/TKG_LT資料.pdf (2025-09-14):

# TKG LT


## フリー交流会で意見交換したいこと


・TKGの技術紹介
PMの伊藤さんがポスターをもってお待ちしてます.
・TKGの活動場所,資金
社会人の皆様どうしてますか？正直困っています.
・TKGでの活動内容・勧誘
→今回はこちらを中心に.
技術紹介ポスター | TKG活動場所 ロンリウムがあと4枚欲しい 保管場所とお金が無い...

## チーム紹介


・チーム名 TKG
└ To-Kai-Group
└ 4社の社会人連合チーム.東海地方を拠点に活動.
・ロボット開発を楽しむことをモットーに活動(ロボコン経験は問いません) →お試しメンバーからガチ勢まで所属(今年度は10人) →大会当日遊びに来るお試し参加でもOK!
・初顔合わせが多く，飲み会や合宿等で交友を深めています．
白馬にスキー合宿 | CoRE2を観戦しながら飲み会

## チーム紹介


・費用はやりたいことに合わせて自己負担
・戦績
└ 2023年:同盟戦優勝，チーム単体では目立った活躍できず…
└ 2024年:同盟戦準優勝，革新的技術賞，リスクアセスメント賞受賞 (前年度よりは同盟戦で仕事ができた？)
└ 2025年:同盟戦優勝，チーム単体でも活躍できた！

前年大会の様子(けいはんなロボット技術センター)

## 開発環境

・日頃のやり取り/打ち合わせ:Discord
・メカ設計環境:Fusion360→来年度はSolid Works? ・ソフト開発環境:ROS2 ，CS+ ，MPLAB X IDE等 ・資料管理:Google Drive，GitHub
https://github.com/TKG-Tou-Kai-Group
・回路設計環境:KiCAD, フリーの回路CAD等
・使用マイコン/SBC:


Jetson Nano, Renesas RX，PIC，NVIDIA Xavier等

居住地/活動場所がバラバラなので，
リモート開発できるようにしています．
(特に制御系は分割)

←GitHub リンク

## 開発環境

・工房＠名古屋市内
└ 2018~2025 10月close予定.社会人有志で立ち上げ(2025現在8名) └ ロボット開発(CoRE，かわロボ，その他各自の活動)，エコランの2チーム └ 主に機械加工/ユニット組立で工房使用
└ CNC卓上フライス，卓上旋盤，ボール盤，バンドソー等基本的なものは何でも ・誤家庭設備(CNC卓上フライス，卓上ボール盤，3Dプリンター等) ・動作確認/評価:誤家庭，会社施設


工房の主力マシン


(魔改造卓上CNCフライス)


制御調整作業
(会社所有の会館)

メカ組立作業
(誤家庭)

参考


開発資料
https://github.com/TKG-Tou-Kai-Group/TKG_Wiki (Twitterにも開発風景UP #CoREjp_TKG)
2022年度機 | 2023年度機

←TKG wiki リンク

## お気軽にお声がけください．

お待ちしています！

←TKG メルアド

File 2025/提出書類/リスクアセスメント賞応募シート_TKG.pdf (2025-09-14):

### The Championship of Robotics Engineers

## リスクアセスメント賞 応募シート

チーム名：TKG (Tou-Kai-Group)

1．リスクアセスメントの目的
ロボット開発環境における危険源を把握し、選手
権に関わる全ての人の事故や災害に至るリスクを設
計段階で可能な限り取り除き、安全なロボット開発
を行う。
2．リスクアセスメントの流れ
CoRE リスクアセスメント表を使用し、ロボット
設計、作業環境、動作試験・練習時などのリスクアセ
スメントを実施した。リスクアセスメントのフロー
を右図に示す。
3．リスクアセスメントおよび対策結果
リスクアセスメントを実施した結果、初期リスク
レベルⅣ:5 件、Ⅲ:7 件、Ⅱ:2 件の計 14 件を見積も った。その中から一部の内容について、リスク低減
策、措置後のリスク見積もり結果を抜粋して示す。
3.1 射出部ローラの安全カバー
カテゴリ:
ロボット設計、初期リスクレベル:Ⅳ
(S:10,F:2,Q:3)
内容:
フライングディスク射出部はローラを高速回転さ


せてフライングディスクを発射する構造のため、回転の遠心力でローラが破損・分解 した場合、周囲に飛散した部品に当たると重傷を負うリスクがある。
対策:
右図のようにローラの外側にアルミ製フレ
ームを設置し、フレームに樹脂製カバーを
取り付けることで、ローラが破損した場合
でも周囲に部品が飛散しないようにした。
措置実施後のリスクレベル:
II(CoRE 安全管理の規則を満たす)
3.2 CNC フライス盤削り出し部品の両面面取り
カテゴリ:

フレーム; 樹脂製カバー; ローラ

作業環境/動作試験･練習、初期リスクレベル:Ⅲ(S:1,F:4,Q:3)
内容:
CNC フライス盤を使用してエンドミルで削り出した部品は、バリによって稜線部が 非常に鋭利になっており、触れた際に切り傷を負う可能性がある。
対策:
部品加工時に、上下両面に対して
面取り加工の工程を追加すること
で、バリを除去した。加工後の部
品写真を右図示す。
措置実施後のリスクレベル:
II(CoRE 安全管理の規則を満たす)

部品に面取り加工を追加

3.3 運搬台車のロボット固定部
カテゴリ:
作業環境/動作試験・練習、初期リスクレベル: Ⅲ(S:3,F:3,Q:4)
内容:
ロボットの運搬・組立調整時に使用している台車について、ロボットの保持部が木製 のため滑りやすく、作業中にロボットが転倒する恐れがある。
対策:
ロボット保持部にクッション材を追加することで、ロボットと台車間の摩擦力を大き くして滑りにくくした。
措置実施後のリスクレベル:
II(CoRE 安全管理の規則を満たす)
3.4 工作機械の安全カバー
カテゴリ:
作業環境、初期リスクレベル:Ⅳ(S:10,F:1,Q:4)
内容:
ロボットの部品製作に CNC フライス盤を使用することがあるが、加工中に切削液や 切粉が飛散する、工具が折れて飛散するといった可能性があり、目に入ると失明のリ スクがある。
対策:
CNC フライス盤に安全カバーを設置し、切削液、切粉、工具の破片が機外に飛散する のを防止した。
措置実施後のリスクレベル:
II(CoRE 安全管理の規則を満たす)

安全カバー; CNC フライス盤

4．リスクアセスメント結果および残留リスクの周知
リスクアセスメント実施にあたっては、項目の抜け・漏れの防止と内容の周知のために 事前に DR を実施し、チーム内で意見の収集と情報共有を行った。また残留リスクの周知 のために、リスクアセスメントシート作成後にチーム内で内容を再度共有し、危険個所の 確認を行った。

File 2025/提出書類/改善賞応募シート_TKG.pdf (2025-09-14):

1 / 3

### The Championship of Robotics Engineers

## 改善賞 応募シート

チーム名：TKG (Tou-Kai-Group)

本文書では、前年度までの課題とそれに対する改善方法を説明する。

1. 概要
弊チームでは、機体の運搬や整備において以下の課題が浮き彫りとなっており、 特定メンバーに負荷が集中する問題が起きている。
・輸送時に分解する必要があるが、分解方法を特定のメンバーしか把握していない ・専門知識や技量が求められる調整箇所が複数存在し特定のメンバーしか調整できない ・射出機構ローラの製造/組立において、多大な工数が掛かっている 以上の背景から、本年度は整備/調整人員の属人化解消を目的とし、誰でも機体の分解や 調整ができるよう改良した。
2. 改良項目
実施した改良項目の概要を表 1 に示す。3 章にて詳細を説明する。
表 1 改良項目
項目 | 種別 | 簡単な説明 | 効果
分解容易化 分解手順明確化 | 恒久対策 | ・マガジンの分解/復帰作業の簡易化 ・運搬時分解ボルトの明確化 | 問題なく運用中
調整不要化 調整方法簡易化 | 恒久対策 | ・射出機構に存在する調整箇所の 廃止や容易化 | 問題なく運用中
組立作業効率向上 | 恒久対策 | ・射出ローラの組立作業効率化 | 問題なく運用中
3. 改良方法の詳細
3.1 分解容易化/分解手順の明確化
弊チームでは、ディスクを格納するマガジンを運搬時に外す運用としている。前年度の マガジン取り付けは、一人がマガジンを持ち上げた状態でもう一人がボルトを固定してい くという不安定な構造であった。この構造では必要人数の課題だけでなく、転倒など安全 面の懸念、射出機構との相対位置バラツキによる性能低下などの課題があった。 そこで本年度は、マガジンが固定部材の上で自立する安定構造とし、上下左右方向とも 位置決めブロックに押し当てることで自動的に位置が決まる設計とした。他の手法として、 専用治具を使った調整が考えられるが、特定人員しか調整できないリスクが残り根本的解 決とならないため、本手法が最もシンプルかつ有効な手法である。 また、誰でも一目で分解箇所が分かるように、分解時に外すボルトにマーキングするこ とで回路・制御ンバーを含めチーム全員が分解/復帰ができようになった。これによって最 小限の工数で大幅な改善ができた

運搬時外すボルトに対して

青マーキング マガジン

位置決めブロック
→これに押し当てて
取り付けることで
毎回同じ位置に取り付く

3.2 射出機構の調整不要化/容易化 射出機構は長時間連続高速回転する部分であり、機構の信頼性が特に求められる。 弊チームの射出機構では下図に示す調整箇所がある。これら全てにおいて当該機構に精通 したメンバー2 人しか調整できなかった(両名とも役職者であり、負荷がより集中)。; ガイドとローラとのクリアランス調整について、 前年度は、ガイドを手で動かしボルトを締める手法であった。ローラとガイドとの微小な; ガイドとローラとのクリアランス調整 近い:抵抗が大きく射速が稼げない 遠い:ローラとの接触が弱く射速が稼げない; →適正な位置に調整が必要; ローラ主軸軸受への予圧; 軸ブレを抑えて射出安定性を高める; ガイド; 軸受寿命 UP による信頼性向上
治具によるガイド位置調整 治具先端にガイドが接触す るように締めることで、 どの場所でも同じクリアランス となる。
穴あけ・インシュ ロック通し治具 同時に行えること で工数大幅減; 昨年度; 本年度; ゴム キリ インシュロック

2 / 3

距離差が飛距離に大きく左右するにも関わらず微調整が難しく、誤って緩めた場合に再調 整が必要な構造であった。本年度は専用治具の作成およびボルトによる調整方式とするこ とで、ローラとの距離を細かく調整でき、ナットによって位置の再現性を担保した。 主軸予圧方式について、
前年度はねじの締め具合で予圧調整していた。締めすぎると軸受破損に繋がり、不安定な 調整方法であった。本年度は、シンプルかつ有効な手法であるウェーブワッシャを使用し た予圧方式を採用しボルトを締めきれば自動的に適切な予圧がかかる設計を採用した。公 差ばらつきによって予圧量は変わるが、公差の上限/下限値の状態にてばね荷重を計算し、 問題ないことを確認したうえで採用した。

3.3 組立作業容易化


弊チームの射出機構のローラは、中空ゴムをローラに対して結束バンドで縫い付けてい る。前年度までは、最初にキリでゴムに穴を開け、その後結束バンドを通していく手順で あった。素材がゴムのため、開けた穴の収縮により結束バンドが通しづらく、くわえて固 定箇所が 16 ヶ所もあるため、生産に多大な工数を奪われていた。 そこで本年度は、下図に示す穴あけ&結束バンド通し治具を作成/運用とすることで穴あけ と同時に結束バンドが通されるように改善された。製作に際しても下記課題を解決した。 課題①：先端部品とパイプのはめあい精度が緩いと、治具が抜けゴムの中空部に落下 して取れなくなる(中空部に残した場合、回転時に吹っ飛ぶため使用不可) 対策①：接着剤と併用することで、部品同士の接合がはずれないようにした

課題②：大きな穴をあけるとゴムが裂けやすくなるため、パイプは極薄が望ましいが 自作は困難
対策②：精密極細パイプの市販品を探し出し、採用した
運用の結果、約 1 時間の作業時間が約 15 分に短縮された。予備ローラも製作している ため改善効果が非常に大きい。

ウェーブワッシャ
による予圧
ネジを締切れる
構造

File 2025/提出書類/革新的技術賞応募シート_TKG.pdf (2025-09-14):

## The Championship of Robotics Engineers

## 革新的技術賞 応募シート

## チーム名：TKG (Tou-Kai-Group)

本文書では、チーム目標とそれを実現する革新的なアイデアを説明する。なお、革新性を有 するアイデアを青字の下線部(イ)～(ト)で示す。

1. 概要
CoRE2023 の弊チームは、アタッカーの飛距離こそ参加チーム上位であったが、以下の 点から同盟戦では主力として活躍できなかった(右図赤線)。 ・各要素の信頼性が乏しく試合ごとに発揮できる能力にばらつきがあった。 ・車体制御性能が低く相手鎧を正確に狙えなかった。
よって、2023 年度の反省点は「性能を優先した結果、安 定性の育成が不十分であった結果、同盟戦で主力として活 躍できなかった」ことである。よって、2024 年度のチー ム目的を「同盟戦で主力となって活躍できる」こととした。 また、オートタレットの開発を進めるチームが増加して
おり、オートタレットの性能が自同盟の戦力に与える影響 が大きくなると予想される。
以上から、本年度は同盟戦で主力となって活躍するため
にチーム目標を「アタッカー育成、オートタレット開発」 として右図青線のチーム構成を目指す。

1.1 アタッカー育成


アタッカーの育成項目は、「射角」、「位置決め」、「安定性」、「強化素材対応」である。実 績値や他チーム調査結果から、表 1 の目標値を設定し、実現のためのアイデアを提案した。

表 1 アタッカー育成項目
目標 | 機構の概要と実現のためのアイデア
射角 | 本陣上部のダメージ パネルを狙えること | 従来相当の投射能力を有したまま本陣上部のダメージ パネルを狙える跳ね上げ式射角調整機構(イ)
位置決め | 角度制御精度 1deg 以内 | 車体を低速でも精密に制御できる起動トルク補償器(ロ)
安定性 | MTBF※1 3 試合 | インシュロックにかかる衝撃を吸収し て破損を防止するためのローラーゴム 縫い付け用インシュロックへの弾性接 着剤の塗布(ハ)
強化素材 対応 | 回収/設置 20sec 以内 | ラフな車体位置決めでも容易に強化素材を回収できる ハンド部の揺動誘い構造(ニ)

※1 MTBF:Mean Time Between Failure,平均故障間隔

1.2 オートタレット開発
オートタレットには、目標のダメージパネル位置をリアルタイムかつ正確に検出するダメ ージパネル検出、目標位置にボールを当てるために必要なジンバル角度やローラー回転速 度を生成する指令生成、指令に高速かつ正確に追従する機構制御が必要である。

表 2 オートタレット開発項目
目標値 | 機構の概要と実現のためのアイデア
ダメージパ ネル検出 | 検出周期 20Hz | ポジティブ・ネガティブテンプレートを 用いたテンプレートマッチング(ホ)に よる高速・高精度なダメージパネル認識
指令生成 | 有効射程 3m | 空気抵抗を考慮した射出角をルックアップテーブルによる 目標指令(ジンバル角度、ローラ回転数)の生成(ヘ)
機構制御 | 定常偏差 0.7deg 以内 | 静止摩擦力による位置決め精度の劣化を改善するための ジンバル制御における静止摩擦力を考慮した LQR 制御(ト)


2. アタッカー育成の詳細
2.1 跳ね上げ式射角調整機構
昨年までの投射機構では本陣の上側に設置されたダメージパ ネルを狙うことができなかった。そこで、右図の赤枠のように投 射機構の先端部に跳ね上げ式の角度調整機構を取り付ける(イ)こ とで、高いところのダメージパネルを狙えるようにした。通常時 はフライングディスクの威力を減衰させないために”通常時”の ように飛翔するフライングディスクとフライングディスクの経 路(赤線)が干渉しないよう位置決めし、本陣のダメージパネルを 狙う際のみ”跳ね上げ時”のように上向きにフライングディスク を投射することで、相手アタッカー等との交戦時にも従来同等 の投射能力を維持できる機構である。

2.2 起動トルク補償器
投射方向の微調整や、強化素材に対する位
置決めでは車体を微速動作できることが望
ましい。一方、PID 制御器ではモータや地面
の静止摩擦の影響で指令に対する追従性が
低下する。そこで、静止摩擦トルクに相当す


るトルク指令値を始動時にトルク指令値に加算する起動トルク 補償器を実装した。右図のように起動トルク補償器は角速度指 令が 0 から変化した時点を起点に、静止摩擦トルク相当量をト ルク指令値に加算し、一定時間で漸減させる(ロ)ことで右図下段 のように静止摩擦トルクから抜け出しやすくし、低速での制御 性能を改善した。


2.3 ローラーゴム縫い付け用のインシュロックに弾性接着剤を塗布 投射ローラーに取り付けるゴムを固定しているインシ
ュロックが投射ローラーの高速回転時に振動によって外
れる課題があった。そこで、インシュロックのロック部に 弾性接着剤を塗布する(ハ)ことで高速回転時の振動下でも インシュロックが外れなくなり、安定性を向上できた。

2.4 ハンド部の揺動誘い構造
試合中は、短時間で強化素材を回収し据え付ける必要が
ある。そこで、強化素材を回収するハンド部に受動的な揺 動構造を設ける(ニ)ことで対処した。
具体的な構造を右図に基づき説明す
る。右図の赤枠内がばねを有する受動
的な蝶番である。強化素材と接触して
いない状態のハンドは右図(a)の状態
にある。それに対して、強化素材と接
触しその移動方向と把持方向一致しな
かった場合には右図(b)赤矢印のよう
にハンド全体が受動的に揺動すること
で進行方向にずれがあっても強化素材
を回収できる。


3. オートタレット開発の詳細
3.1 ポジティブ・ネガティブテンプレートを用いたテンプレートマッチング ダメージパネルの検出は可能な限り高速であることが望ましい。一方、オートタレット の計算資源は限られるため、AI による手法よりも古典的な画像処理を用いることが適切で ある。しかし、典型的な手法であるテンプレートマッチングは、ロボットの移動によるダ メージパネルの角度変化によって、カメラ画像中のダメージパネルとテンプレート画像と の類似度が逐次変化するため、安定した検出が難しかった。 そこで、カメラ画像から対象のダメ
ージパネルの LED の色のみを色抽出画
像として抽出し、その画像に対して、ダ
メージパネルの LED の存在確率密度分
布（ポジティブテンプレート,右図中央）
と非存在確率密度分布（ネガティブテ
ンプレート,右図右）をテンプレートと
してテンプレートマッチングを行う(ホ)
ことで、柔軟性の確保と誤検出の低減
を実現した。


3.2 空気抵抗を考慮したローラー回転数指令およびジンバル角度指令の生成 オートタレットから発射されたボールは、短距離では初等物理における斜方投射問題の 解析解に従う。しかし、飛距離が長くなるにつれ空気抵抗の影響を無視できなくなるため、 ローラー回転数やジンバル角度を算出するためには、空気抵抗を考慮する必要がある。一 方、空気抵抗を考慮した場合は解析的に解
くことは難しく、最適化計算により近似解
を求める手法も計算時間がかかりリアル
タイム性を維持することができない。そこ
で、予め計算したルックアップテーブルを
用いることで空気抵抗を考慮したローラ
ー回転数およびジンバル角度の指令生成
を実現(ヘ)した。これにより、右図の同一射
角における投射距離と到達高度の関係に
おいて、青線の空気抵抗を考慮した到達位
置の予測による指令生成を実現し、リアル
タイム性も確保した。

3.3 静止摩擦力を考慮した LQR 制御

空気抵抗を考慮する 空気抵抗を考慮しない 到達地点(空気抵抗あり) 到達地点(空気抵抗なし)

遠距離までボールを正確に命中させるためにはローラー回転数とジンバルの角度の制 御が重要となる。例えば、6m 先のダメージパネル(□150mm)に命中させるためには誤差 0.7 (≒atan((0.15/2)/6))度以下の位置決め性能が必要である。しかし、微小範囲の位置決め は摩擦力、特に静止摩擦力によりその位置決め性能が劣化することが知られており、前記 性能を達成するための阻害要因となっている。一方、サンプルとなる姿勢制御プログラム は PID 制御を使用しており摩擦がある場合も定常偏差なく制御できるが、最適なパラメー タ調整に職人技が必要であり、調整に膨大な工数が必要となる。 そこで、最適制御手法の一種である LQR 制御によりパラメータ調整工数を削減しつつ、 LQR 制御単体では静止摩擦力によって生じる残差を、静止摩擦力をハイパボリックタン ジェントと動き出し開始時点を 0 度した角度θを用いた式(1)により算出したトルクTs( 指令角速度)をフィードフォワードトルクとして補償(ト)することで、0.5 度以内まで残差を 減らすことができた。
Ts(指令角速度) = −最大静止摩擦力 × exp (

指令角速度
ストライベック角速度)

2
tanh (

θ
ε

) ⋯ (1)

ε:十分に小さい値

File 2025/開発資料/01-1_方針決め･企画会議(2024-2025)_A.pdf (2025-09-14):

# CoRE2024-2025 方針決め･企画･構想

## TKG 伊藤(万)

やること
自己紹介
チーム方針・方向性決め(確認)
要素開発アイテム決定
└ 特に新人さんにトライ頂くアイテム
ラフなスケジュール
担当決め


### 実施日:2024/6/9 (Discord) A改訂:2024/6/10 (会議結果を踏まえて修正)

# 自己紹介シート

## ~/2025/99_その他/Scrambleロボコン_自己紹介_2024-2025.xlsx

# 自己紹介

# おさらい/大会概要

# ・挑戦的共創人材を輩出する場としてのロボットエンジニア選手権 ・主催:一般社団法人 次世代ロボットエンジニア支援機構 様

# ・他のロボコンと異なり，”チームメンバー”にも焦点を当てている． └ 個人表彰制度有り ・一人称視点操縦&同盟 ・2023~2025テーマ:天下統一ロボットバトル ・社会人も参加OK ・2025/3 第3回大会開催予定@京都市(島津アリーナ)

## https://scramble-robot.org/

## https://core.scramble-robot.org/

## 大会公式HP

初回参加者向け

# 開発の流れ

DR1:構想審査; →Output:構想設計書; DR2:外部設計審査; →Output:外部設計書; DR3:詳細設計審査; →Output:詳細設計書(全体ASSY); 方向性決め; アイデア出し・要件定義; 構想設計(外部設計); 詳細設計(内部設計); DR4:評価結果審査; →Output:評価報告書，試合戦略; └ 機構確定，使用モータ･センサ確定; └ 詳細構造完成，以後製造．; 本年度は流用部多く，構想審査は不要とする．

大会

昨年度

昨年度

昨年度

4

初回参加者向け

# ロボット概要/構成要素 初回参加者向け

## マガジン(MG)


自機

└ ディスクを溜め込む
└ 射出機構へディスクを送る

## 射出機構

ディスク

## 強化素材アーム

(23年度未実装)
足回り | └ 強化素材の回収/設置
└ オムニ足x4

Realsense D435

## サブカメラ(x2) └ 2D全周視野

RICOH THETA

## メインカメラ(照準)

水平2軸アーム+ハンド

### 操縦画面

弾着予測円
距離情報

## 制御盤

## 鎧(HP)

//その他
HDMIトランスミッター
受信機

2023年度機で説明

# 2024年度方針

【目標】

# ・同盟戦で主戦力となって活躍 ・賞を沢山取る

【機体】

# 一通りの機能を持つ万能型の開発 └ 基礎機能+強化素材取り扱い ※基礎機能:トラブルなく走る，撃てる． 賞の受賞 └ 革新的技術賞はmust，個人表彰も取りたい．

【運営】

# 評価期間/練習期間を十分確保． └ 年末前後で完成 └ 最低機能必達とし年末で遅延しているものは切り捨て ※最低機能:昨年度相当 └ 流用部分多いため，変更点起因のトラブルを避ける．

└ DRBFM等&&他の人が気付けるようにする

反省会で決めたため，ここではおさらい．

前回:万能タイプを開発．初回よりは活躍．
強化素材取り扱い機能は間に合わず．

前回:革新的技術賞とリスクアセスメント賞受賞．
全チーム内トップレベルの受賞数．

前回:1/E時点で完成しなかったら保険機適用
→守れず(いけそうと判断&変更点管理が甘かった)

前回:賞を沢山取る→2賞受賞，目標ほぼ達成．
(個人表彰は取れず)

# 機体構成


重心偏り

重心真ん中に

200 100

前回
・マガジン自動交換を想定したレイアウト
・強化素材把持位置，射線を機体中心線上に配置
→偏った重心位置になり，射高ダウン．
足のサスペンションを殺して無理やり射高調整した結果， 様々な不具合発生．
・強化素材アーム/ハンドは間に合わず．
・2Dアラウンドビュー(全周視野)実装．

今回:
・自動交換廃止し，重心が真ん中に来るレイアウトに．
・強化素材アーム/ハンドの実装
・射高調整機構の実装(使わないかもしれないが付けておく) ・アラウンドビュー継続(2D継続 or 3D化)
・外装こだわる(FRPでカウル作成等)

・制御盤位置も変更か
・機構シフト量は仮値
・鎧は四隅にしたい
・外装カバー付ける
└ アームにも付ける

マガジン
自動交換

マガジン手動交換

ずらし量は未定

# UI系

# 【前回の2Dアラウンドビュー】 ・性能面:非常に優秀 ・会場の無線HDMIと接続し辛い(相性？振動？)

【今回】

# ・接続トラブル問題→サス有効化で振動低減．相性問題は保留．

・3D化

# └ 3D化のメリット:敵味方識別，狙われているか分かる ・衝突防止機能 └ 未定．警告表示 ～ 車体停止に介入(後者の場合，緊急回 避操作時に停止される可能性もある．やる場合は操作優先度や安 全性などを考慮して決める)

土方さんと進め方相談して決定．
会議で決定したことは追記する．

https://dreamvu.com/pal-usb/

# 制御系(下位レイヤー)

【計画】
仕様抽出 7月E ※メカ側要件が固まり次第。
射出の角度制御する場合は、ラジコンサーボ用にPWMインターフェースを2つ用意する？ 制御系説明会(佐藤) 7月M
CAN通信によるモータ制御の検証(桑田) 7月E
基板の仕様決め(桑田・生田) 8月M
基板の設計(生田) 8月E
基板試作(生田) 9月M
モータ・センサ単体でのソフトウェア実装(桑田) 9月E

【備考】
・桑田さん，生田さん，大塚さんにも入って頂く．
└ 組込みS/W:桑田さん，大塚さん？，基板設計･製造:生田さん ・ハンド(アーム)制御は別途制御基板を用意する。
(１つの基板に詰め込むと複数人での平行開発が難しいため) ・オシロは購入。費用はチーム負担か、個人負担か費用清算のタイミングで決める。 (チーム負担なら工房行？)

# やることリスト

## 参考)改善点リスト ~/2025/01_企画･構想/前年度からの改善点リスト.xlsx

# 必要な要素開発

## ~/2025/01_企画･構想/やることリスト_240607.xlsx ●

佐藤さんサポートのもと，
射出/強化素材取り扱い系の
回路＆制御をやって頂く．

別途説明の場を設ける

# 担当割り振り

メカ

# └ 全体見る人:伊藤 └脚:田上，製造は日髙/伊藤 └射出/マガジン(MG):阿部 ※方向制御機構含む └アーム:田上，新規の場合:伊藤or阿部or●● └ハンド:田上，●● └外装:？※年明けやるイメージ．負荷状況次第．

H/W

# └ 佐藤，生田

S/W

# └ 佐藤，桑田，大塚，UI系:土方

# 役職割り振り

【役職】

# 監督(SV):(田上さん or 阿部さん or 誰か)？※監督は他役職兼任不可なので注意． キャプテン(CAPT):伊藤 プロジェクトマネージャー(PM):日髙さん 安全:田上さん？ 阿部さん続投でも良い． 広報:日髙 or 佐藤 or 伊藤

# 【競技役職】 総大将(なった場合):監督以外 操縦手:mustは監督以外&&操作練習できる方(遠方でない) wantはゲーマー(FPS等) →日髙さん？ (田上さん) 装填手:阿部さん？佐藤さん？

左記役職を設けるルールとなっています．
灰色部は今決めなくて良い．
取りまとめは本会議にて決定する．

※安全担当
ガチでやるなら安全指針が出せる人＆チェックできる人
＆全体設計に関わる人
→伊藤or阿部or日髙．日髙さんは監督なら兼任不可．

個人的に阿部さん推薦

# スケジュール(案)

構想DR; 外部仕様DR 詳細DR; ルール発表; 機体完成 (3/17); 射出評価; 方針決め 企画; 外部仕様 DR; 【要素】 射高(ジャンプ台); 3D-View; 構想DR省く？ ・射高調整機能有無 ・UI系(2D or 3D); 議論して決める; 要素評価結果反映; ルール変更内容が気になるが， 大幅な設計変更を強いられることはないとする． あったらその時考える． ルール発表を待たず製造する．; ルール発表想定; 回路完 (全体評価できる状態); メカ完; (公式提供物実装完); 詳細DR; ポイント: 年末までにロボットが動く状態にする(全組状態で動作確認ができる); 射出制御系，アーム系

# (参考)前年度企画会議でのスケジュール

今年

## 前回計画

## 前回実績

└ 本機

└ 保険機
└ 要素

構想 DR1 (構想審査); 詳細 DR2 (外部仕様審査); 製造 DR3 (詳細設計審査); (評価結果審査); 検証の余裕なし; (外部仕様審査); (構想審査); (詳細設計審査); ﾍﾞﾝﾀﾞｰ製造/評価/改良; ルール発表; 大会本番; DR1(構想審査); ルール発表次第で戦略変更→仕様変わるかも？ ということで9/Fに構想審査; 外部仕様検討 要素設計; DR2 (外部仕様審査); DR3 (詳細設計審査); 内部設計 要素設計仕上げ; 全体ASSY設計; 最終調整 大会準備; DR4 (評価結果審査); (一部は先行組立) 基本となる足回りなど; フリスビーばらつき; ※8/5の意見交換会の結果を踏まえて計画策定

# 保険機で大会を迎えることがないように！

14

# 予算計画

【目標】

# 全体:50万

# 【割振り】


## ガチ勢の中で分担(諸事情考慮しガチ勢内の分担比率調整)

## お試し参加はゼロ(当日交通費/宿泊費，チームパーカー代¥4,000は集めます)

## 前回(本機50+他20予算)

前回

議論して目標決める

UI系次第か？
(メカ出費は前回より大幅減見込む)


直近To Do 議論して決める(項目追加/削除/変更，緑字部更新)

【全体】

## 計画表作成:日髙(~6/E) 【本機検討】

全体レイアウト:伊藤(~6/E) ※重心，鎧入るか，アーム改造有無

## MG変更:阿部(7/F~7/E) 足制御改良:佐藤(~/) 制御系引き継ぎ:佐藤⇒~6/E:仕様出し，7/F実機見学，7/M 制御系の説明会 【要素検討】 3D View実現性:土方(~7/M~E(外仕DR前))

H/W変更検討(UI):土方 ※Xavier変えるなら

## 射高変更評価:伊藤，日髙(~6/E，7/F評価(実機見学7/6. 7/7評価)) ハンド改良/評価:田上，伊藤 (現実性確認~7/F) ※別途田上さんと会話します

【製造】

## 足ユニット量産:伊藤，日髙 (~8/E) 【その他】 顔合わせ飲み会やります7/6→良いお酒の飲み方を教える 名古屋のほうが良い

# 直近To Do

全体計画:計画表作成[日髙]
制御系(佐藤さんサポートのもと，桑田さん、生田さん(基板製造のお手伝い)にも入って頂く) 6/30 引き継ぐためにセンサリストと流用基板の仕様（足周り）を展開
7/7 どういったものか不明なためロボットを見せる
7/14or20 制御系説明会を実施
~7/E CAN通信によるモータ制御の検証[桑田]
~7/E 仕様抽出 ※メカ側要件が固まり次第

オシロは購入。費用はチーム負担か、個人負担か費用清算のタイミングで決める。チーム負担なら工房行？ ハンド改良・アーム
田上さん7/Fまでに現実性を確認
MG改良/射出改良、非常停止、HDMIトランスミッター、無線、パトライト、HPインジケータ配置 阿部さん（～7/30)
鎧・カメラ配置
伊藤さん(～6/30）
CADは無料版みんなでできるか試してみる
7/6ジャンプ台、左右方向調整の搭載 火入れは7/7に実施。

# 開発環境

# ・資料管理:Google Drive ・メカ設計:Autodesk Fusion360 (個人課金+無料) ・H/W設計:KiCAD ・H/W使用:Jetson Nano，Renesas RX，NVIDIA Xavier，

### ラズパイ等 ※これに拘らない

# ・S/W設計:Renesas CS+, ROS2等 ※これに拘らない ・製造:メカは工房，誤家庭設備 基板は中国(elecrow) ・評価:小幡会館(三菱電機)，大隈会館(オークマ)，誤家庭

H/W, S/Wはだいぶ変わるかも？

# モットー

# ・楽しむこと └ デスマになりそうなら機能切り捨て．睡眠大事． └ 他のライフイベントや他の趣味と両立．

### ※大会直前でも旅行優先したりしてました．

# ・メンバーは平等 └ 役職者が偉いわけではないです． └ DRは設計をレビューするのであって，発表者をレビューするのではない．

## 学生時代のようなデスマはしません！

# 議事録

・補足
今年度の開催場所は島津アリーナ京都
自動照準をどう実装するか（車体制御介入か、画面表示だけか）はカメラ入手次第決める 車体制御だと回路構成が変わってくる？3D-Viewは7/Eに実現性確認 uiのH/Wはそのまま

## ・やること分担

制御系
桑田さん、生田さん(基板製造のお手伝い)に引き継ぐ
日程案は佐藤さんから
6/30 引き継ぐためにセンサリストと流用基板の仕様（足周り）を展開 7/7 どういったものか不明なためロボットを見せる
7/14or20 制御系説明会を実施
~7/E CAN通信によるモータ制御の検証

9/E デバッグ開始

オシロは購入。費用はチーム負担か、個人負担か費用清算のタイミングで決める。チーム負担なら工房行？ ハンド改良・アーム
田上さん7/Fまでに現実性を確認
MG改良/射出改良、非常停止、HDMIトランスミッター、無線、パトライト、HPインジケータ配置 阿部さん（～7/30)
鎧・カメラ配置
伊藤さん(～6/30）
CADは無料版みんなでできるか試してみる
7/6ジャンプ台、左右方向調整の搭載 火入れは7/7に実施。

参考

# 開発資料


# https://github.com/TKG-Tou-Kai-Group/TKG_Wiki (Twitterにも開発風景UP #CoREjp_TKG)

2022年度機 | 2023年度機

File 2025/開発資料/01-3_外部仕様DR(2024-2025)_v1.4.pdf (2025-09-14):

# CoRE2024-2025 外部仕様DR

### TKG 伊藤(万)

やること
・外部仕様の決定


・(レビュー結果を受けて)外部仕様変更箇所の明確化
・スケジュール共有
・担当共有

実施日:2024/8/25(日) 20:00~@Discord
V1.0 初版作成[伊藤]
V1.1 DR結果で変更になった点＆議事録を追加[伊藤] V1.2 足のモータをロボマスモータに変更［日高］
V1.3 ロボマスモータ化に伴う制御系の構成変更[佐藤] V1.4 基板構成の見直し[佐藤]

DR1:構想審査; →Output:構想設計書; DR2:外部仕様審査; →Output:外部仕様設計書; DR3:詳細設計審査; →Output:詳細設計書(全体ASSY); 方向性決め; アイデア出し・要件定義; 構想設計(外部仕様); 詳細設計(内部仕様); DR4:評価結果審査; →Output:評価報告書，試合戦略修正; Now

大会


# 開発の流れ

※大会運営に提出する資料ではありません．

# TKG-CoREプロジェクト全体概要(参考) [伊藤]

## Output

ロボ本体+操縦画面; 表彰制度; 本DR対象; 設計へFB; 事前検証; 技術資産; (資料，コード，モデル); 表彰ネタ; 他チーム; TKGのロボコン活動; 外部公開; 使用者の声; 相互交流による; 人材育成; (土方さん); チーム内交流; CoREシミュレータ; Isaac Sim; 8/25追記 自動機も開発するかも (メカ・HWは公式提供され， SWのみチームで開発する 固定砲台の方)

全体構成 | [伊藤]
本機 | 操縦画面


距離情報

弾着予測円

足回り
└ オムニ足x4
└ ダンパー追加

鎧

射出機構
└ ローラー+加速ガイド
└ 仰角調整機構追加

マガジン(MG)
└ ディスクを溜め込む
└ 射出機構へ
ディスクを送る
└ 手動交換

TKGロゴ

ディスク

強化素材アーム
&ハンド

正面カメラ
(照準)

360°カメラx2
(2D全周視野
生成用)

2D全周視野

正面カメラ映像

輸送時の分解
伊藤カーでも運べるように設計する．
→射出，MG，アーム，鎧，カメラは外す．
足ユニットは外さない．

制御盤位置
機体正面から見て左側～MG下を想定．

全体構成 | [伊藤]


重心偏り

前年度
・マガジン自動交換を想定したレイアウト
・強化素材把持位置，射線を機体中心線上に配置
→偏った重心位置になり，射高ダウン．
足のサスペンションを殺して無理やり射高調整した結果， 様々な不具合発生．
・強化素材アーム/ハンドは間に合わず．
・2Dアラウンドビュー(全周視野)実装．

今年度
・重心バランスを考慮したレイアウト
・ユニットのバランスを考慮(鎧は対角，MGは機体幅の真ん中) ・強化素材取り扱い機能の実装
・射出仰角調整機能の実装
・2Dアラウンドビュー継続(3Dはカメラ来ず断念)
※今年度で手動機は完成させ，次年度以降異なる
種別のロボを開発できるようにしておく(やるかは未定)

機体中心を
重心に

強化素材取り扱いアーム/ハンド
→未実装

仰角調整
鎧，強化素材機構に
干渉しない

強化素材機構
鎧，仰角調整機構に
干渉しない．アーム収
納時に機体に収まる．

### 【機構概要】 ・4輪オムニ+ダンパー


足回り | [田上→日髙]

### ・モータ：M3508P19 ・モータドライバ：RoboMaster C620 ・バネ定数計算

¥ (https://drive.google.com/open?id=14CAs_uDYy9d-VlVm4dtHXjaAQxGyQDkE&usp=drive_fs)¥ (https://drive.google.com/open?id=14CAs_uDYy9d-VlVm4dtHXjaAQxGyQDkE&usp=drive_fs)Scramble- (https://drive.google.com/open?id=14CAs_uDYy9d-VlVm4dtHXjaAQxGyQDkE&usp=drive_fs)CoRE (https://drive.google.com/open?id=14CAs_uDYy9d-VlVm4dtHXjaAQxGyQDkE&usp=drive_fs)¥ (https://drive.google.com/open?id=14CAs_uDYy9d-VlVm4dtHXjaAQxGyQDkE&usp=drive_fs)2025 (https://drive.google.com/open?id=14CAs_uDYy9d-VlVm4dtHXjaAQxGyQDkE&usp=drive_fs)¥ (https://drive.google.com/open?id=14CAs_uDYy9d-VlVm4dtHXjaAQxGyQDkE&usp=drive_fs)02_ (https://drive.google.com/open?id=14CAs_uDYy9d-VlVm4dtHXjaAQxGyQDkE&usp=drive_fs)詳細検討 ¥ (https://drive.google.com/open?id=14CAs_uDYy9d-VlVm4dtHXjaAQxGyQDkE&usp=drive_fs)01_ (https://drive.google.com/open?id=14CAs_uDYy9d-VlVm4dtHXjaAQxGyQDkE&usp=drive_fs)足回 (https://drive.google.com/open?id=14CAs_uDYy9d-VlVm4dtHXjaAQxGyQDkE&usp=drive_fs)り (https://drive.google.com/open?id=14CAs_uDYy9d-VlVm4dtHXjaAQxGyQDkE&usp=drive_fs)･ (https://drive.google.com/open?id=14CAs_uDYy9d-VlVm4dtHXjaAQxGyQDkE&usp=drive_fs)フレーム (https://drive.google.com/open?id=14CAs_uDYy9d-VlVm4dtHXjaAQxGyQDkE&usp=drive_fs)¥ (https://drive.google.com/open?id=14CAs_uDYy9d-VlVm4dtHXjaAQxGyQDkE&usp=drive_fs)バネ定数検討 (https://drive.google.com/open?id=14CAs_uDYy9d-VlVm4dtHXjaAQxGyQDkE&usp=drive_fs).pdf (https://drive.google.com/open?id=14CAs_uDYy9d-VlVm4dtHXjaAQxGyQDkE&usp=drive_fs)

### 【制御要求事項】 ・動力計算シート

¥ (https://docs.google.com/spreadsheets/d/14Cb5rqqmi___hLgb0iJKlrWQRHaVFv7e?rtpof=true&usp=drive_fs)¥ (https://docs.google.com/spreadsheets/d/14Cb5rqqmi___hLgb0iJKlrWQRHaVFv7e?rtpof=true&usp=drive_fs)Scramble- (https://docs.google.com/spreadsheets/d/14Cb5rqqmi___hLgb0iJKlrWQRHaVFv7e?rtpof=true&usp=drive_fs)CoRE (https://docs.google.com/spreadsheets/d/14Cb5rqqmi___hLgb0iJKlrWQRHaVFv7e?rtpof=true&usp=drive_fs)¥ (https://docs.google.com/spreadsheets/d/14Cb5rqqmi___hLgb0iJKlrWQRHaVFv7e?rtpof=true&usp=drive_fs)2025 (https://docs.google.com/spreadsheets/d/14Cb5rqqmi___hLgb0iJKlrWQRHaVFv7e?rtpof=true&usp=drive_fs)¥ (https://docs.google.com/spreadsheets/d/14Cb5rqqmi___hLgb0iJKlrWQRHaVFv7e?rtpof=true&usp=drive_fs)02_ (https://docs.google.com/spreadsheets/d/14Cb5rqqmi___hLgb0iJKlrWQRHaVFv7e?rtpof=true&usp=drive_fs)詳細検討 ¥ (https://docs.google.com/spreadsheets/d/14Cb5rqqmi___hLgb0iJKlrWQRHaVFv7e?rtpof=true&usp=drive_fs)01_ (https://docs.google.com/spreadsheets/d/14Cb5rqqmi___hLgb0iJKlrWQRHaVFv7e?rtpof=true&usp=drive_fs)足回 (https://docs.google.com/spreadsheets/d/14Cb5rqqmi___hLgb0iJKlrWQRHaVFv7e?rtpof=true&usp=drive_fs)り (https://docs.google.com/spreadsheets/d/14Cb5rqqmi___hLgb0iJKlrWQRHaVFv7e?rtpof=true&usp=drive_fs)･ (https://docs.google.com/spreadsheets/d/14Cb5rqqmi___hLgb0iJKlrWQRHaVFv7e?rtpof=true&usp=drive_fs)フレーム (https://docs.google.com/spreadsheets/d/14Cb5rqqmi___hLgb0iJKlrWQRHaVFv7e?rtpof=true&usp=drive_fs)¥ (https://docs.google.com/spreadsheets/d/14Cb5rqqmi___hLgb0iJKlrWQRHaVFv7e?rtpof=true&usp=drive_fs)駆動系メカ仕様検討 (https://docs.google.com/spreadsheets/d/14Cb5rqqmi___hLgb0iJKlrWQRHaVFv7e?rtpof=true&usp=drive_fs).xlsx (https://docs.google.com/spreadsheets/d/14Cb5rqqmi___hLgb0iJKlrWQRHaVFv7e?rtpof=true&usp=drive_fs)

フレーム高さ = 75mm

フレーム高さ = 40mm

8/25追記 | 自重中立位置で65mm
中立位置は変更なし．
載る機構側に調整代は設ける．
(昨年より調整幅持たせます)

給弾/射出機構 | [伊藤]

### 全体構成


機構概要
・給弾アーム+射出ローラ+仰角調整
・モータ
└ 射出ローラ
maxon DCX35L + 歯車速比1.2
└ トルク計算

~/2025/02_詳細検討/2024年度メカ検討資料.xlsx
└ 給弾アーム:DJI GM6020
└ 仰角調整:近藤のラジコンサーボ
(KRS786 or KRS4034)

制御要求事項
・回転数パターン3段階(評価して決める)
└ 動作確認用低速，高速，超高速
・給弾アームは2位置制御(前回のままで)
・仰角パターン複数段(評価して決める)
└ -側1poit(水平射出時),
└ +側1point

仰角調整
(新規構想部分)

射出ローラ
(基本流用)
・ゴム膨張抑制
(インシュロック種類，本数)

給弾アーム

構成は流用．新規構想部分は緑字で表示．
本陣上部の鎧攻撃用に仰角調整機能設ける．

足フレームとの接続フレーム
新レイアウトに合わせて設計し直し
Maxon固定板も変わる

保険機

→8/25追記
2位置だけで良いのでソレノイド駆動にする．

給弾/射出機構 | [伊藤]

### 仰角調整

仰角板に歯を切る; モータ; 回転中心 滑走面; 仰角板; 滑走面 隙間; →8/25追記 可動側は滑走面を固着させる必要無いのでは？ ゴムとかで引っ張とけば良さそう． ⇒そのようにする．

先行評価では上図のように滑走面が連続な構造にした．
単純にサーボでやろうとすると下図が最もシンプルだが，
必ず滑走面が不連続になる．これを無視して良いのか，
連続であるべきなのかが分からない．or 他に良い方式があれば…
上図&&サーボでやるなら上図をベースに右図のような構造を考えている．

マガジン | [阿部]


### 【機構概要】 ・装弾数25枚ｘ2列=50枚 ・2列目をタイミングベルトによる 直動機構で送り出す ・装弾のため前面を開き戸とする

### 【制御要求事項】 使用モータ：M2006(変更無し) 原点（退避側）にリミットスイッチ使用 動力計算シート

¥ (https://docs.google.com/spreadsheets/d/1i27chjT2-uGtM_OPX-HJ69h74gX-sWsH/edit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)¥ (https://docs.google.com/spreadsheets/d/1i27chjT2-uGtM_OPX-HJ69h74gX-sWsH/edit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)Scramble- (https://docs.google.com/spreadsheets/d/1i27chjT2-uGtM_OPX-HJ69h74gX-sWsH/edit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)CoRE (https://docs.google.com/spreadsheets/d/1i27chjT2-uGtM_OPX-HJ69h74gX-sWsH/edit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)¥ (https://docs.google.com/spreadsheets/d/1i27chjT2-uGtM_OPX-HJ69h74gX-sWsH/edit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)2024 (https://docs.google.com/spreadsheets/d/1i27chjT2-uGtM_OPX-HJ69h74gX-sWsH/edit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)¥ (https://docs.google.com/spreadsheets/d/1i27chjT2-uGtM_OPX-HJ69h74gX-sWsH/edit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)02_ (https://docs.google.com/spreadsheets/d/1i27chjT2-uGtM_OPX-HJ69h74gX-sWsH/edit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)詳細検討 (https://docs.google.com/spreadsheets/d/1i27chjT2-uGtM_OPX-HJ69h74gX-sWsH/edit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) ¥ (https://docs.google.com/spreadsheets/d/11IIrZ3ln8DoJUry3jkay27bCIQTSwFFS/edit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)03_MG (https://docs.google.com/spreadsheets/d/11IIrZ3ln8DoJUry3jkay27bCIQTSwFFS/edit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)¥ (https://docs.google.com/spreadsheets/d/11IIrZ3ln8DoJUry3jkay27bCIQTSwFFS/edit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)MG (https://docs.google.com/spreadsheets/d/11IIrZ3ln8DoJUry3jkay27bCIQTSwFFS/edit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)仕様検討 (https://docs.google.com/spreadsheets/d/11IIrZ3ln8DoJUry3jkay27bCIQTSwFFS/edit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)v3.xlsx (https://docs.google.com/spreadsheets/d/11IIrZ3ln8DoJUry3jkay27bCIQTSwFFS/edit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)

開

閉

主な変更点; ・取付角度+90°変更

・自動交換廃止→シャッタを開き戸に変更

→射出機構と干渉するため，射出機構との相対位置(Z)を+10mm?移動 ・押し棒ガイドまわり信頼性向上(根元の剛性UP)

扉の固定はパッチン錠．2ヶ所付けると締め忘れ&ディスク送り出し不良につながるので1ヶ所で行う方針．

強化素材取り扱い | [伊藤]

### 全体構成


構成
単軸直動アーム
+自動把持/着脱ハンド
主な変更点
・アーム機構変更:
水平旋回2軸アーム
→直動単軸アーム

※水平2軸アームトルク不足のため
・ハンド信頼性向上:
把持部2ヶ所，ローラ径UP等

ハンド設計
サイズ制約

強化素材アクセス方向

強化素材回収
アーム展開→車体前進&自動把持
→巻き上げ→アーム収納
強化素材設置
アーム展開→スポット上に車体移動
→巻き下げ→車体後退&自動開放
※デプスカメラの距離情報も活用

射線，把持位置は
一直線にする．
デプスカメラも合わせる．
(前回同様)

強化素材取り扱い | [伊藤]


アーム | 【機構概要】 ・単軸直動 └ リニアガイド+タイミングベルト(S5M相当品) ・モータ:DJI M3508P19+C620 └ 速比38(仮) 1:19x1:2(歯車) └ トルク計算シート(未) ~/2025/02_詳細検討/2024年度メカ検討資料.xlsx ・センサ等:LSx2
| 【制御要求事項】

・想定動作
①LS1基準でストローク端までアーム前進
②強化素材回収
③原点までアーム後退
※初期位置はLS1反応位置．電源ON時そこを原点に． ※LS2が反応しちゃったらそれ以上いかないようにする (ストローク端はLS2が反応しない位置にするが，
原点ズレが発生した際にLS2で保護する)
※メカストッパも設けます(LS反応位置+15mm程度)

リニアガイド
└ MGN9C600コンパチ
(MGから流用)

S5M 1225

M3508P19

アイドラ

歯車減速
(1:2~1:3)

移動部

1.5kg目標+ハンド●kg

LS1

LS2

8/25修正
・LS1基準での位置制御
+アーム展開状態で保持制御(位置，速度)
・LS2はリミット用

# 強化素材取り扱い

### アームの可動配線取り回し


[伊藤]

方式 | 信頼性 | 重量 | コメント
ぶらり配線 | △ | ○ | 重量的にメリット大きいが，配線が暴れるため危険． 暴れを簡単に抑止できるならこっちで考えたい．
ケーブルベア | ○ | △ | 確実だが重くなる&部品点数が増える． ハンドのモータ1系統のためだけに使うのは勿体ない．

配線支持棒
これだけのための棒は重量的に勿体ないので，
実際はMG固定用フレームなどから伸ばすのが良いか

8/25追記
簡易的なケーブルベアにする．
⇒薄い樹脂シートをU字型にしてケーブルベアとする．

# 強化素材取り扱い


ハンドですが、再選定したモーター仕様で外観は作れました。 (Fusionに慣れてないので内部データは多分ひどいことになってます。) スライドはなるはやで作ります。すみません
→Fusion独特なので，ゆっくり慣れていきましょう！ 私も最初は戸惑いました．一番最初に触れたCADに体が慣れてしまうんですよね…

### ハンド

[竹内]

https://www.amazon.co.jp/dp/B003B2DP4C?tag=note0e2 a- (https://www.amazon.co.jp/dp/B003B2DP4C?tag=note0e2a-22&linkCode=ogi&th=1&psc=1)22&linkCode=ogi&th=1&psc=1 (https://www.amazon.co.jp/dp/B003B2DP4C?tag=note0e2a-22&linkCode=ogi&th=1&psc=1)

ローラの滑り止め候補

・たいまつ保持は1ヶ所で行う(図の通り)
・サイズ制約は把持中心でΦ150→詳細はDidcordチャット確認． 図ははみ出ているので歯車かます．NCで削る．
・ハンドの誘いは現行設計で十分か？
→スポット側の穴隙間で不十分であれば，アーム側に揺動機能追加． ・ローラの滑り止め固定方法はインシュロックを想定．

UI系 | [土方]

距離情報 └ 敵/構造物との距離把握 └ 強化素材取り扱い時の操縦補助; アラウンドビュー(2D) └ 周囲把握による操縦補助 └ 同盟戦司令部への情報提供; ※360°カメラ2台の映像から生成; 弾着予測円 └ 攻撃時の操縦補助 └ かっこよさ; 前回の仕様のまま流用; TKGロゴ; 下記情報は追加しますか？ (To 佐藤君) ・残弾 ・回転数mode ・射出仰角mode ・バッテリ残圧警告 ※Xaivierと通信できるか次第

UI系 | [土方]

## HW構成

前回の仕様のまま流用; 操縦ブース内; Jetson Xavier; Realsense D435; RICOH THETA; 2Dアラウンドビュー生成用360°カメラ; 正面ビュー用(照準等); HDMI Transmitter(送信); HDMI Transmitter(受信); 操縦画面; 分配，合成処理等; ロボット内; マガジン上; 制御盤内

全体構成/制御-HW | [佐藤(取りまとめ)]

測距センサx1 (残弾数把握); 走行制御系 (RX631); 射出&たいまつ 制御系 (PIC); 給弾アーム GM6020; 投射ホイール DCX35L 仰角調整SOLx1; UI系 (Jetson); 操縦者; 受信機; HDMI トランスミッタ; RealSense D435; PC->送信機; 非常停止ボタン; 電源制御基板; バッテリ; 各MDへ; リミットSWx2 (MG装填); MG装填M2008; たいまつアーム (M3508(DJI) x1 DCモータ x1 センサ数:LSx2); 制御箱; ※M3508&C620(DJI)x4; ※全制御基板に入力; RICOH THETA x2

全体構成/制御-制御箱 | 未完成
[佐藤(取りまとめ)]

走行制御基板

射出&たいまつ
制御基板

Jetson

主制御箱

バッテリ(5V)-1
(Jetson用)

バッテリ(24V)-1

(公式)
電源制御基板

電源制御基板
・24V通電制御
・5V生成

MDC30C
×1
(投射ホイール)

MD
(未定,たいまつアーム)

8/25追記
・盤設計は日高さん．

担当

プロジェクト管理:日髙
全体/メカ取りまとめ:伊藤
HW/SW取りまとめ:佐藤
メカ要素設計
└ 足回り:日髙，田上
└ 給弾/射出/仰角調整:伊藤
└ マガジン・無線機器固定:阿部
└ 強化素材取り扱い:伊藤(アーム)，竹内(ハンド) └ 鎧/カメラ:?(負荷状況みて決める)
└ カメラコネクタ固定の信頼性向上:竹内
└ 全体ASSY:(mainは伊藤・日髙)?, 各自 HW/SW
└ 走行系:佐藤
└ 射出系/強化素材系:桑田，生田，大塚
└ UI系:土方
└ 盤設計:日髙
製造
└ メカ:日髙，伊藤，阿部
└ 基板:生田(main)，佐藤
アプリ開発・自動機
└ CoREシミュレータ:土方

//役職メモ(本DRで決めなくてOK)
監督:田上? ※監督はフィールドに入れない．
キャプテン:伊藤
PM:日髙
広報:
安全:
操縦手:愛知勢&&監督以外
装填手:阿部?

ピットメンバー(緊急時ロボ弄る人．監督はNG)
must:佐藤, 土方，(桑田 or 生田 or 大塚), メカ2人 ※HW, SW優先

[伊藤]

※田上さんは11月から復帰見込み

8/25追記
・DR結果を踏まえて修正しました(青字)
・9月中に詳細設計完了．これが遅れると後半厳しい．

スケジュール | [日髙]


~/2025/01_ (https://drive.google.com/open?id=14EozeItVEeTHopiA77V-5HLfsMZTmJ7h&usp=drive_fs)企画 (https://drive.google.com/open?id=14EozeItVEeTHopiA77V-5HLfsMZTmJ7h&usp=drive_fs)･ (https://drive.google.com/open?id=14EozeItVEeTHopiA77V-5HLfsMZTmJ7h&usp=drive_fs)構想 (https://drive.google.com/open?id=14EozeItVEeTHopiA77V-5HLfsMZTmJ7h&usp=drive_fs)/01- (https://drive.google.com/open?id=14EozeItVEeTHopiA77V-5HLfsMZTmJ7h&usp=drive_fs)2_ (https://drive.google.com/open?id=14EozeItVEeTHopiA77V-5HLfsMZTmJ7h&usp=drive_fs)スケジュール (https://drive.google.com/open?id=14EozeItVEeTHopiA77V-5HLfsMZTmJ7h&usp=drive_fs).pdf (https://drive.google.com/open?id=14EozeItVEeTHopiA77V-5HLfsMZTmJ7h&usp=drive_fs) | ●

8/25追記
・9月中に詳細設計完了できるかが肝！

直近To Do | [日髙/伊藤]

・アーム/カメラ関係：現行ハンドと強化素材，カメラを引き継ぐ．佐藤→竹内． ・足フレームの情物一致:
伊藤→穴位置のスケッチ作成．過去CADモデルからトレース 日髙→伊藤スケッチと実物の一致/不一致をチェック→3Dモデルに反映． ・CoREシミュレータテスト 8/31. 愛知から大阪 遠隔操作テスト

全体ASSYモデル作成場所を共通アカウントへ移行
・各機構はそれぞれのプロジェクトで設計→都度全体ASSYに反映 ※ジョイントは全体ASSYのスケッチ基準でお願いします． 他の機構基準だとモデル変更の際にジョイントエラーを吐いて再定義する手間が発生するため． ・全体ASSY直下でパーツのアセンブリは避けてください． ※全体ASSYごと更新の際に面倒になる，直下ファイルが増えると全体ASSYの可読性が悪くなるため．

全体ASSY
└ 機構A ASSY
└ 機構B ASSY
└ …

OK

全体ASSY
└ 機構A ASSY
└ 機構B parts A
└ 機構B parts B
└ 機構B parts …
NG

8/25追記
・DR結果を踏まえて修正しました(青字)

# DR議事録 8/25追記 ・DR議事録を追加しました．

・足の中立位置は変更あるか。（伊藤さん）
→無い。バネ定数を変えたら変わる予定。（日高）
・仰角調整機構のアクチュエータは何にするか。（伊藤さん） →角度は何パターン作る？(佐藤さん）
→敵機、本陣の2パターン（伊藤さん）
→12Vに落とせばラジコンサーボは使えそう。（佐藤さん） →2パターンだけなのでソレノイドを使う。（伊藤さん） ・ガイドの剛性UPはやる？（伊藤さん）
→やります。押棒を剛性UP予定。（阿部さん）
・扉の固定方法はどうなってる？剛性が心配。（日高）
→パッチン錠でやります。（阿部さん）
→二か所つけると忘れてしまうので1個でお願いします。（佐藤さん） ・アームは位置、速度制御で押し切った状態を保持する。（佐藤さん） ・アームは移動部を分解するほうが移動が楽。（佐藤さん） ・ケーブル脈動対策はPPシートにする。（伊藤さん）
・リニアガイドは600mm？（伊藤さん）
→はい。（阿部さん）
・軸の保持は何を使えばいいか（竹内さん）
→イモネジか クランプ式（伊藤さん）
・ギヤの作成は3Dプリンタか（竹内さん）
→NCフライス。（日高）
・ハンドのたいまつ保持部は1か所。
・ハンドの誘いは現行設計で十分か。（竹内さん）
→ステージ側の穴でガイドされそう。ダメだったらアーム側が横方向に逃げるようにする。（伊藤さん） ・滑り止めはどう固定するか。接着だと曲率がきつそう（日高）
→結束バンドで。（竹内さん）
・カメラ固定に必要な要素（カメラ保持、ケーブル保持）を佐藤さんから竹内さんに引き継ぐ ・足フレームの穴位置確認を日高で対応
・射出評価のため、目標を決めたい（日高）
→去年の交戦距離から有効射程は3m、その時の高さ方向のブレをダメージパネルの設置高さの範囲 ±50mm。

回路変更点
ソレノイド1つ（射出角度用）、リミットスイッチ2点（アーム用）

# 議事録/困りごとメモ/フリーメモ [各位]

//全体ASSYツリー
全体ASSY[伊藤/日髙]
└ Flame ASSY (脚フレーム)[日髙]
└ Omuni ASSY
└ 射出機構ASSY[伊藤]
└ (各Sub ASSY) ※仰角調整含む
└ MG ASSY[阿部]
└ (各Sub ASSY)
└ 直動アームASSY[伊藤]
└ (直動アーム側の各Sub ASSY)[伊藤]
└ ハンドASSY[竹内]
└ 鎧ASSY(公式鎧モデルを基準スケッチに合致させたもの) └ 中間フレームASSY ※MG固定フレーム等[阿部？] └ 鎧フレームASSY ※鎧&THETA固定用フレーム[？]
└ カメラ固定フレームASSY ※Realsense固定[竹内？]
└ 制御盤ASSY[日髙]
└ 無線ASSY ※MG側に無線Sub ASSY含めてもOK[阿部]
└ (フィールドオブジェクト類) ※本機モデルと関係ないので全体ASSY直下でOK

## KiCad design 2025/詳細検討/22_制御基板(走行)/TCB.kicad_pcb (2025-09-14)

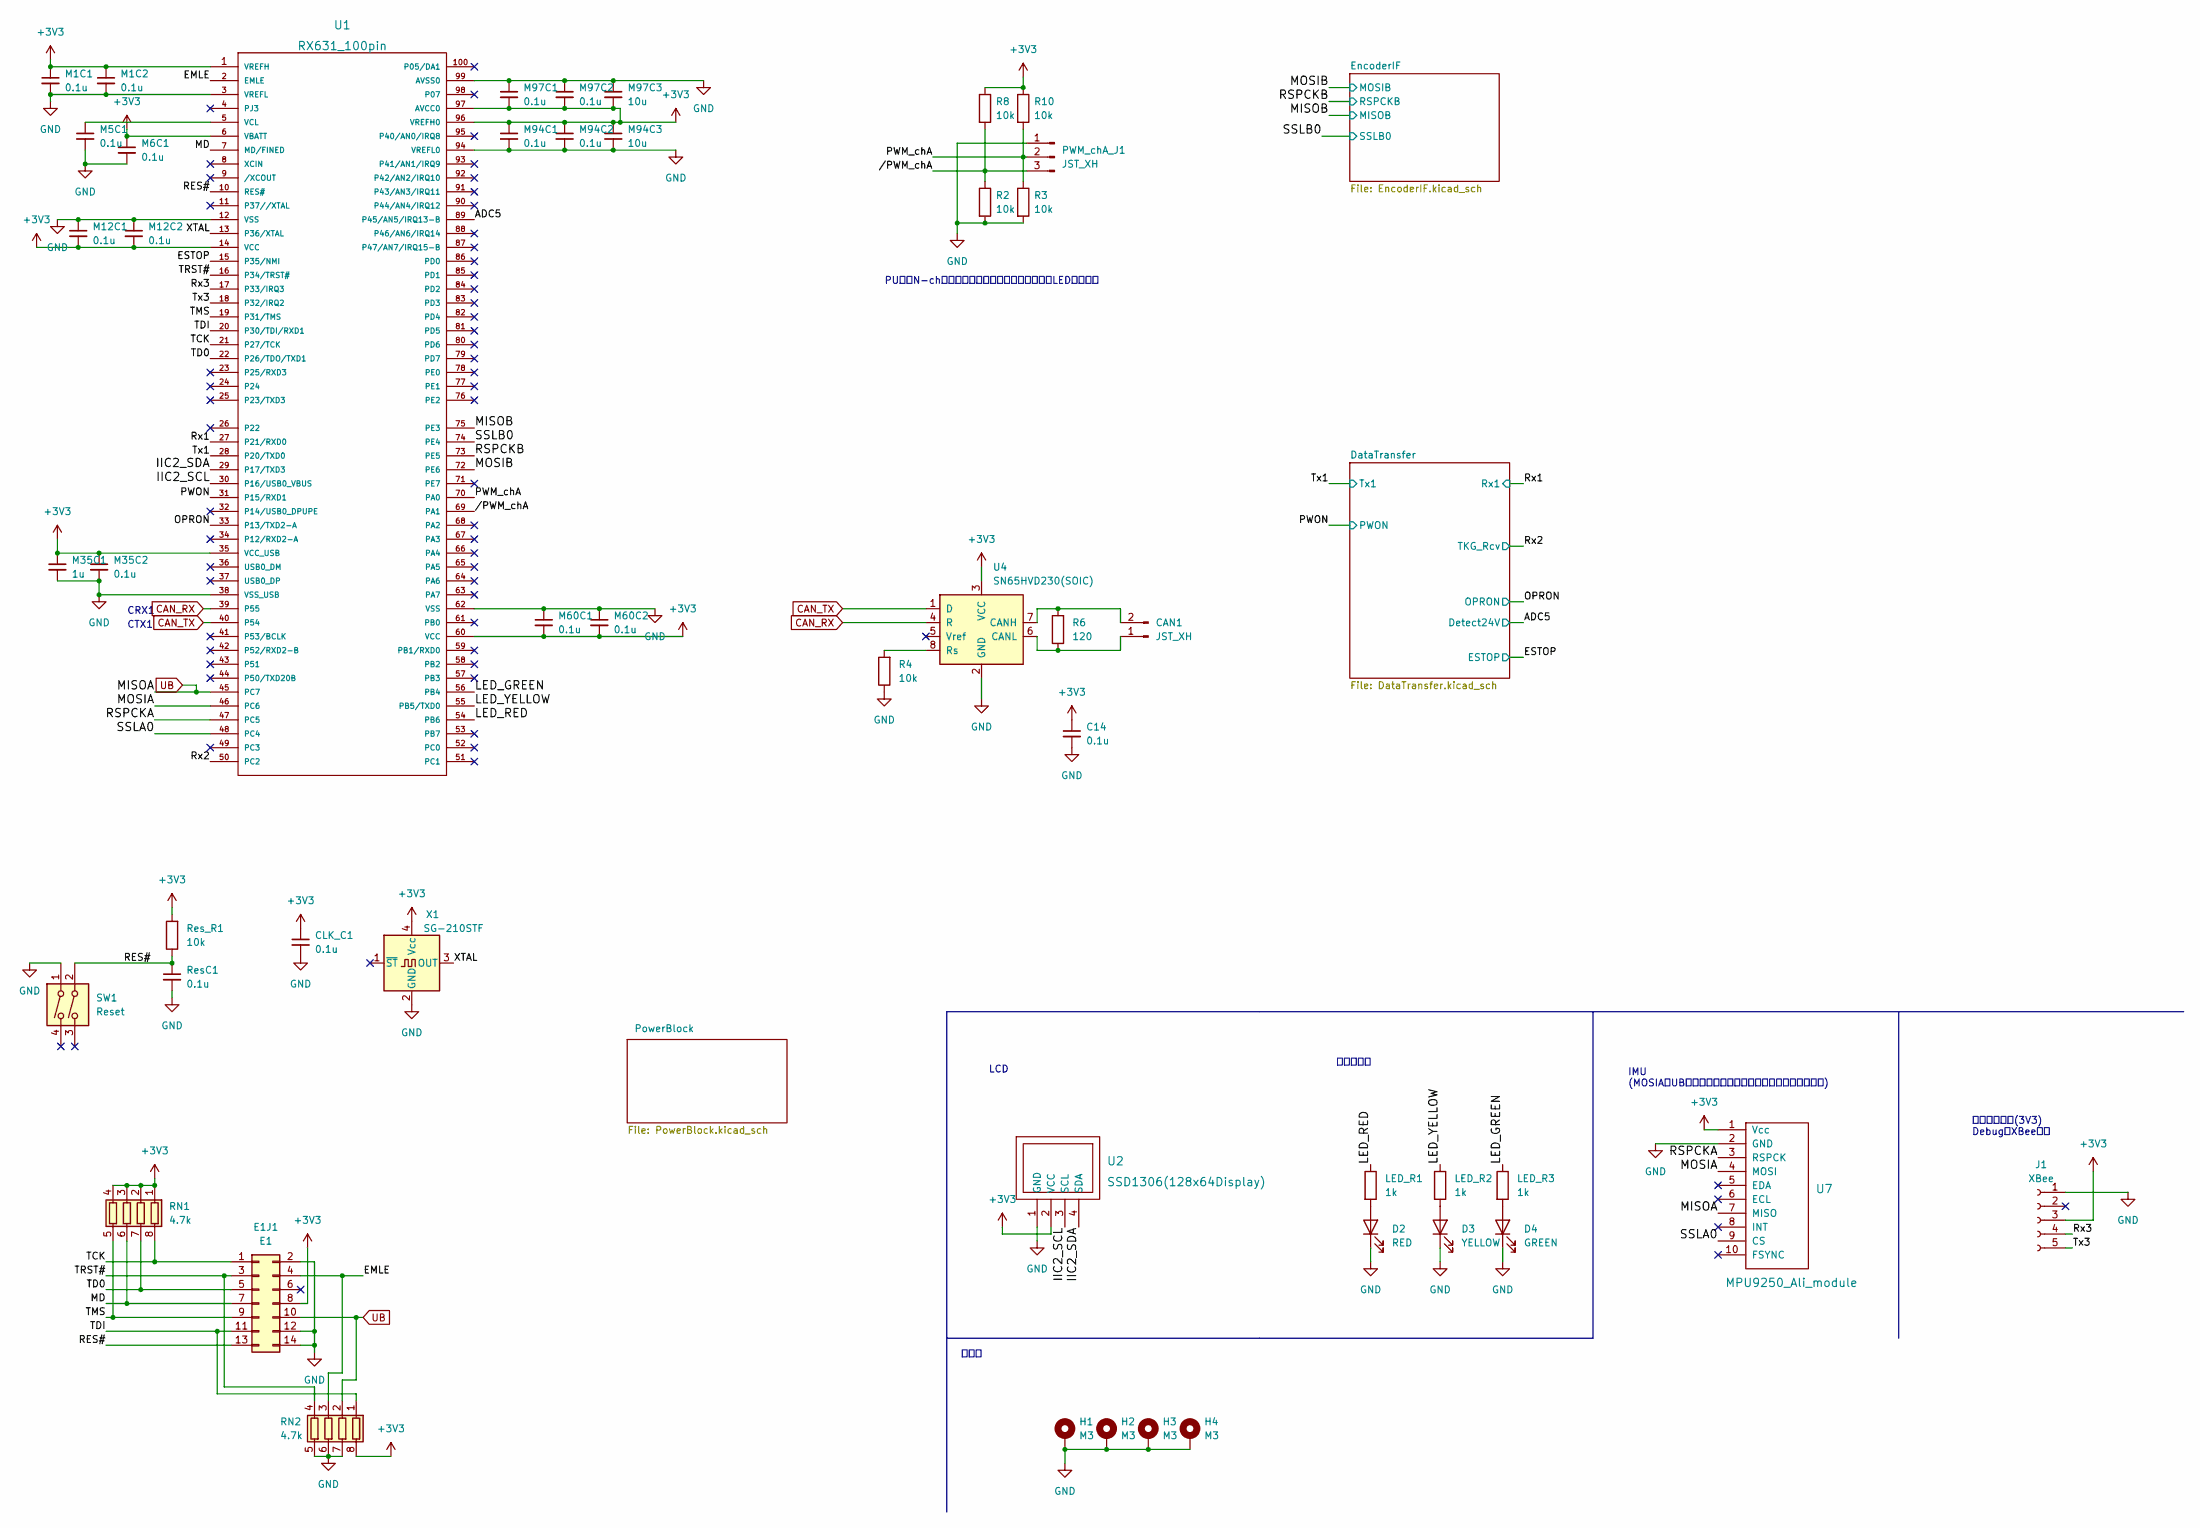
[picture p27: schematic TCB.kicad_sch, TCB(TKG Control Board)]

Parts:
C14: 0.1u; C_0402_1005Metric_Pad0.74x0.62mm_HandSolder
CAN1: JST_XH; JST_XH_B2B-XH-A_1x02_P2.50mm_Vertical
CLK_C1: 0.1u; C_0402_1005Metric_Pad0.74x0.62mm_HandSolder
D2: RED; LED_0603_1608Metric_Pad1.05x0.95mm_HandSolder
D3: YELLOW; LED_0603_1608Metric_Pad1.05x0.95mm_HandSolder
D4: GREEN; LED_0603_1608Metric_Pad1.05x0.95mm_HandSolder
E1J1: E1; IDC-Header_2x07_P2.54mm_Vertical
H1, H2, H3, H4: M3; MountingHole_3.2mm_M3_ISO14580_Pad
J1: XBee; PinSocket_1x05_P2.54mm_Vertical
LED_R1, LED_R2, LED_R3: 1k; R_0603_1608Metric_Pad0.98x0.95mm_HandSolder
M1C1, M1C2, M5C1, M6C1, M12C1, M12C2, M35C2, M60C1, M60C2, M94C1, M94C2, M97C1, M97C2: 0.1u; C_0402_1005Metric_Pad0.74x0.62mm_HandSolder
M35C1: 1u; C_0603_1608Metric_Pad1.08x0.95mm_HandSolder
M94C3, M97C3: 10u; C_0603_1608Metric_Pad1.08x0.95mm_HandSolder
PWM_chA_J1: JST_XH; JST_XH_B3B-XH-A_1x03_P2.50mm_Vertical
R2, R3, R4, R8, R10: 10k; R_0603_1608Metric_Pad0.98x0.95mm_HandSolder
R6: 120; R_0603_1608Metric_Pad0.98x0.95mm_HandSolder
RN1, RN2: 4.7k; R_Array_Concave_4x0402
ResC1: 0.1u; C_0402_1005Metric_Pad0.74x0.62mm_HandSolder
Res_R1: 10k; R_0603_1608Metric_Pad0.98x0.95mm_HandSolder
SW1: Reset; SW_Tactile_Straight_KSA0Axx1LFTR
U1: RX631_100pin; LQFP-100_14x14mm_P0.5mm
U2: SSD1306(128x64Display)
U4: SN65HVD230(SOIC); SOIC-8_3.9x4.9mm_P1.27mm
U7: MPU9250_Ali_module; PinSocket_1x10_P2.54mm_Vertical
X1: SG-210STF; Oscillator_SMD_SeikoEpson_SG210-4Pin_2.5x2.0mm

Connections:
+3V3: C14.1, CLK_C1.1, E1J1.8, J1.3, M1C1.1, M1C2.1, M6C1.1, M12C1.2, M12C2.2, M35C1.1, M35C2.1, M60C1.2, M60C2.2, M94C1.1, M94C2.1, M94C3.1, M97C1.2, M97C2.2, M97C3.2, R8.1, R10.1, RN1.1 (R1.1), RN1.2 (R2.1), RN1.3 (R3.1), RN1.4 (R4.1), RN2.8 (R1.2), Res_R1.2, U1.1 (VREFH), U1.6 (VBATT), U1.14 (VCC), U1.35 (VCC_USB), U1.60 (VCC), U1.96 (VREFH0), U1.97 (AVCC0), U2.2 (VCC), U4.3 (VCC), U7.1 (Vcc), X1.4 (Vcc); also elsewhere on the board
/ADC5: U1.89 (P45/AN5/IRQ13-B); also elsewhere on the board
/EMLE: E1J1.4, RN2.3 (R3.1), U1.2 (EMLE)
/ESTOP: U1.15 (P35/NMI); also elsewhere on the board
/IIC2_SCL: U1.30 (P16/USB0_VBUS), U2.3 (SCL)
/IIC2_SDA: U1.29 (P17/TXD3), U2.4 (SDA)
/LED_GREEN: LED_R3.1, U1.56 (PB4)
/LED_RED: LED_R1.1, U1.54 (PB6)
/LED_YELLOW: LED_R2.1, U1.55 (PB5/TXD0)
/MD: E1J1.7, RN1.6 (R3.2), U1.7 (MD/FINED)
/MISOB: U1.75 (PE3); also elsewhere on the board
/MOSIA: U1.46 (PC6), U7.4 (MOSI)
/MOSIB: U1.72 (PE6); also elsewhere on the board
/OPRON: U1.33 (P13/TXD2-A); also elsewhere on the board
/PWM_chA: PWM_chA_J1.2, R3.1, R10.2, U1.70 (PA0)
/PWON: U1.31 (P15/RXD1); also elsewhere on the board
/RES#: E1J1.13, ResC1.1, Res_R1.1, SW1.2, U1.10 (RES#)
/RSPCKA: U1.47 (PC5), U7.3 (RSPCK)
/RSPCKB: U1.73 (PE5); also elsewhere on the board
/Rx1: U1.27 (P21/RXD0); also elsewhere on the board
/Rx2: U1.50 (PC2); also elsewhere on the board
/Rx3: J1.4, U1.17 (P33/IRQ3)
/SSLA0: U1.48 (PC4), U7.9 (CS)
/SSLB0: U1.74 (PE4); also elsewhere on the board
/TCK: E1J1.1, RN1.8 (R1.2), U1.21 (P27/TCK)
/TD0: E1J1.5, RN1.7 (R2.2), U1.22 (P26/TDO/TXD1)
/TDI: E1J1.11, RN2.1 (R1.1), U1.20 (P30/TDI/RXD1)
/TMS: E1J1.9, RN1.5 (R4.2), U1.19 (P31/TMS)
/TRST#: E1J1.3, RN2.4 (R4.1), U1.16 (P34/TRST#)
/Tx1: U1.28 (P20/TXD0); also elsewhere on the board
/Tx3: J1.5, U1.18 (P32/IRQ2)
/XTAL: U1.13 (P36/XTAL), X1.3 (OUT)
//PWM_chA: PWM_chA_J1.3, R2.1, R8.2, U1.69 (PA1)
CAN_RX: U1.39 (P55), U4.4 (R)
CAN_TX: U1.40 (P54), U4.1 (D)
GND: C14.2, CLK_C1.2, D2.1 (K), D3.1 (K), D4.1 (K), E1J1.2, E1J1.12, E1J1.14, H1.1, H2.1, H3.1, H4.1, J1.1, M1C1.2, M1C2.2, M5C1.2, M6C1.2, M12C1.1, M12C2.1, M35C1.2, M35C2.2, M60C1.1, M60C2.1, M94C1.2, M94C2.2, M94C3.2, M97C1.1, M97C2.1, M97C3.1, PWM_chA_J1.1, R2.2, R3.2, R4.1, RN2.5 (R4.2), RN2.6 (R3.2), RN2.7 (R2.2), ResC1.2, SW1.1, U1.3 (VREFL), U1.12 (VSS), U1.38 (VSS_USB), U1.62 (VSS), U1.94 (VREFL0), U1.99 (AVSS0), U2.1 (GND), U4.2 (GND), U7.2 (GND), X1.2 (GND); also elsewhere on the board
unnamed: CAN1.1, R6.1, U4.6 (CANL)
unnamed: CAN1.2, R6.2, U4.7 (CANH)
unnamed: D2.2 (A), LED_R1.2
unnamed: D3.2 (A), LED_R2.2
unnamed: D4.2 (A), LED_R3.2
unnamed: M5C1.1, U1.5 (VCL)
unnamed: R4.2, U4.8 (Rs)
UB: E1J1.10, RN2.2 (R2.1), U1.45 (PC7), U7.7 (MISO)

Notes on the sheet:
IMU (MOSIAはUB端子経由でプルアップされていることに注意)
CRX1
CTX1
LCD
状態表示灯
取付穴
PUしてN-chオープンドレイン出力とすることでLED駆動する
シリアル通信(3V3) Debug用XBee接続

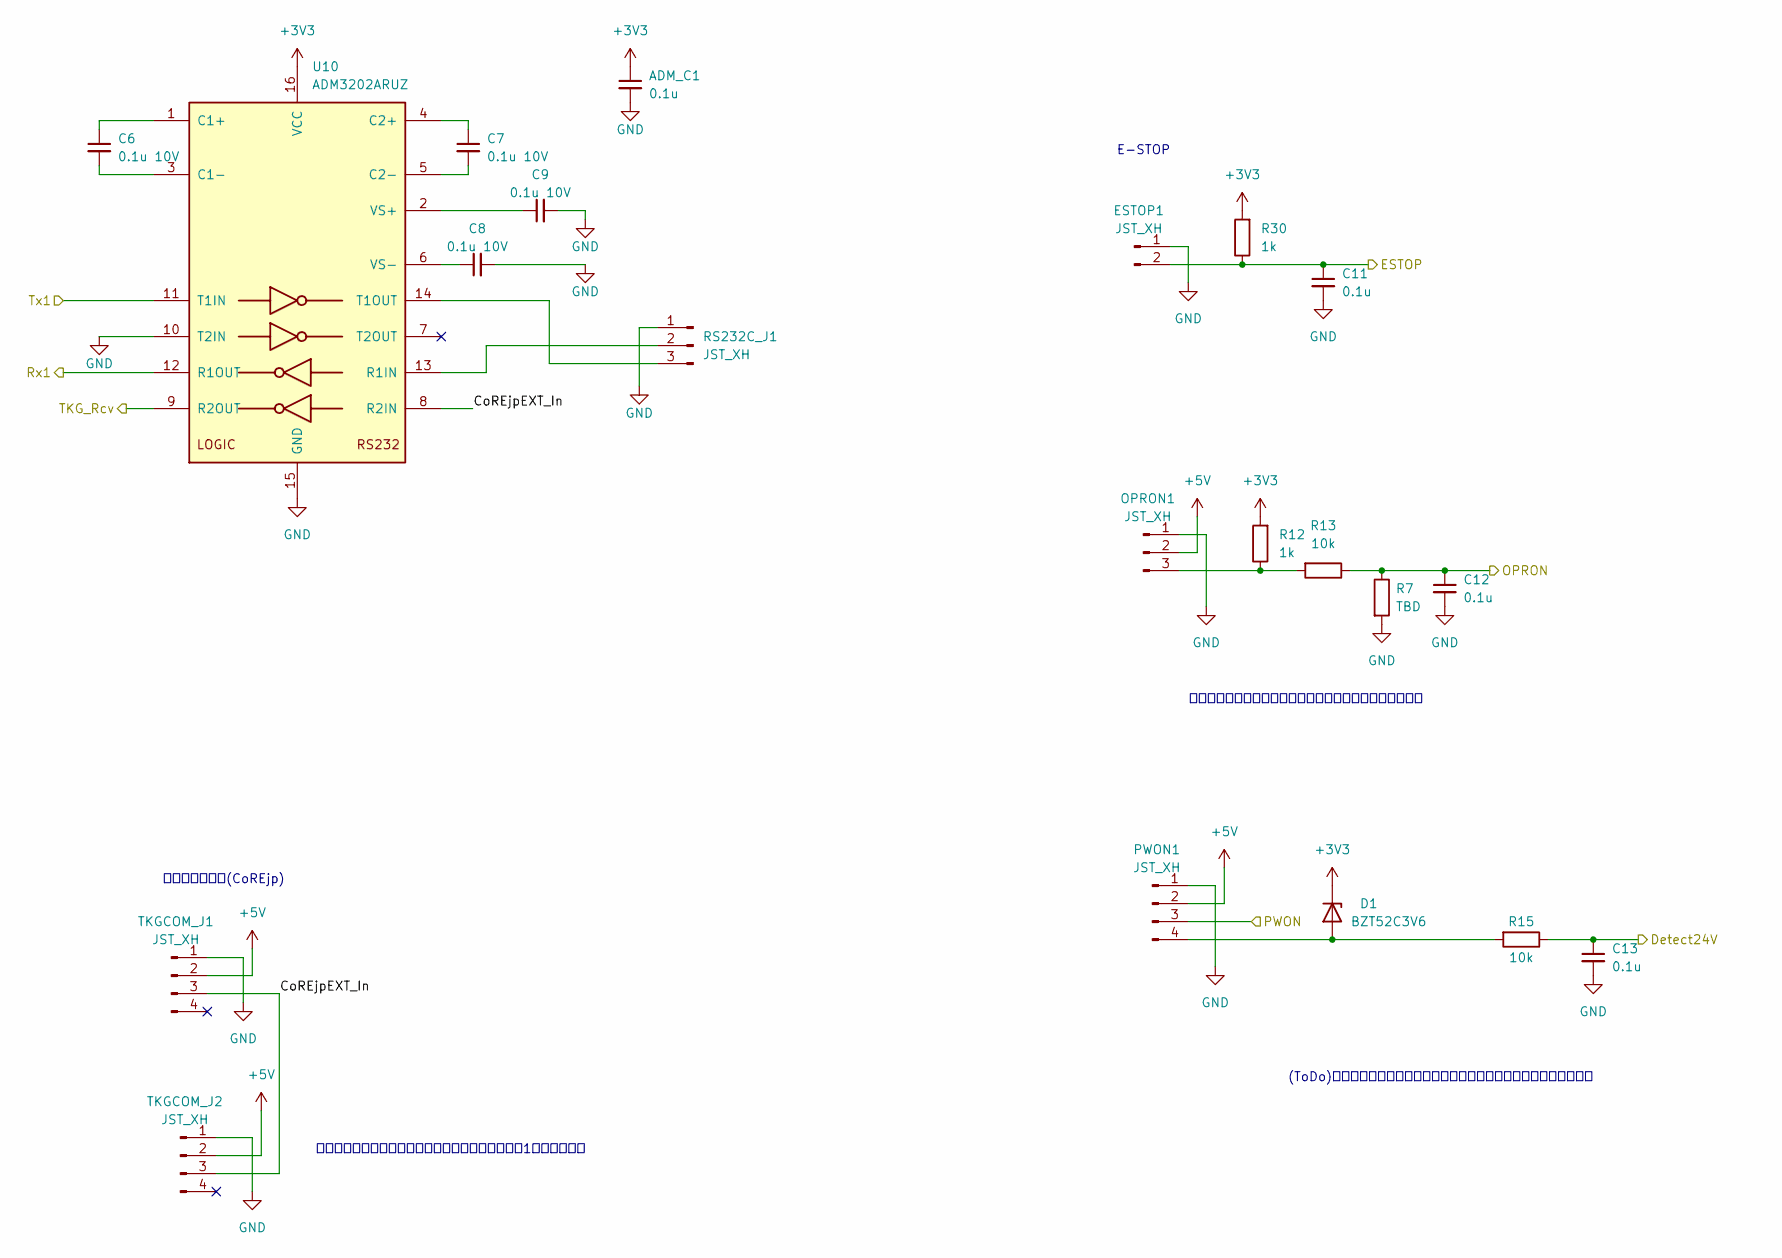
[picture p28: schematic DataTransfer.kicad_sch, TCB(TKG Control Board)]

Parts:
ADM_C1: 0.1u; C_0402_1005Metric_Pad0.74x0.62mm_HandSolder
C6, C7, C8, C9: 0.1u 10V; C_0402_1005Metric_Pad0.74x0.62mm_HandSolder
C11, C12, C13: 0.1u; C_0603_1608Metric_Pad1.08x0.95mm_HandSolder
D1: BZT52C3V6; R_0805_2012Metric_Pad1.20x1.40mm_HandSolder
ESTOP1: JST_XH; JST_XH_B2B-XH-A_1x02_P2.50mm_Vertical
OPRON1: JST_XH; JST_XH_B3B-XH-A_1x03_P2.50mm_Vertical
PWON1: JST_XH; JST_XH_B4B-XH-A_1x04_P2.50mm_Vertical
R7: TBD; R_0603_1608Metric_Pad0.98x0.95mm_HandSolder
R12, R30: 1k; R_0603_1608Metric_Pad0.98x0.95mm_HandSolder
R13, R15: 10k; R_0603_1608Metric_Pad0.98x0.95mm_HandSolder
RS232C_J1: JST_XH; JST_XH_B3B-XH-A_1x03_P2.50mm_Vertical
TKGCOM_J1, TKGCOM_J2: JST_XH; JST_XH_B4B-XH-A_1x04_P2.50mm_Vertical
U10: ADM3202ARUZ; TSSOP-16_4.4x5mm_P0.65mm

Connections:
+3V3: ADM_C1.1, D1.1 (K), R12.2, R30.2, U10.16 (VCC); also elsewhere on the board
+5V: OPRON1.2, PWON1.2, TKGCOM_J1.2, TKGCOM_J2.2; also elsewhere on the board
/ADC5: C13.1, R15.1; also elsewhere on the board
/DataTransfer/CoREjpEXT_In: TKGCOM_J1.3, TKGCOM_J2.3, U10.8 (R2IN)
/ESTOP: C11.1, ESTOP1.2, R30.1; also elsewhere on the board
/OPRON: C12.1, R7.1, R13.1; also elsewhere on the board
/PWON: PWON1.3; also elsewhere on the board
/Rx1: U10.12 (R1OUT); also elsewhere on the board
/Rx2: U10.9 (R2OUT); also elsewhere on the board
/Tx1: U10.11 (T1IN); also elsewhere on the board
GND: ADM_C1.2, C8.2, C9.2, C11.2, C12.2, C13.2, ESTOP1.1, OPRON1.1, PWON1.1, R7.2, RS232C_J1.1, TKGCOM_J1.1, TKGCOM_J2.1, U10.10 (T2IN), U10.15 (GND); also elsewhere on the board
unnamed: C6.1, U10.1 (C1+)
unnamed: C6.2, U10.3 (C1-)
unnamed: C7.1, U10.4 (C2+)
unnamed: C7.2, U10.5 (C2-)
unnamed: C8.1, U10.6 (VS-)
unnamed: C9.1, U10.2 (VS+)
unnamed: D1.2 (A), PWON1.4, R15.2
unnamed: OPRON1.3, R12.1, R13.2
unnamed: RS232C_J1.2, U10.13 (R1IN)
unnamed: RS232C_J1.3, U10.14 (T1OUT)

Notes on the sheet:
リセット端子が必要になった際に拡張できるように1ピン増やした
公式基板の仕様が不明のため合わせられるようにしておく
(ToDo)ﾌﾟﾙﾀﾞｳﾝ抵抗を外すか、入力インピーダンス計算すること
受信機信号入力(CoREjp)
E-STOP

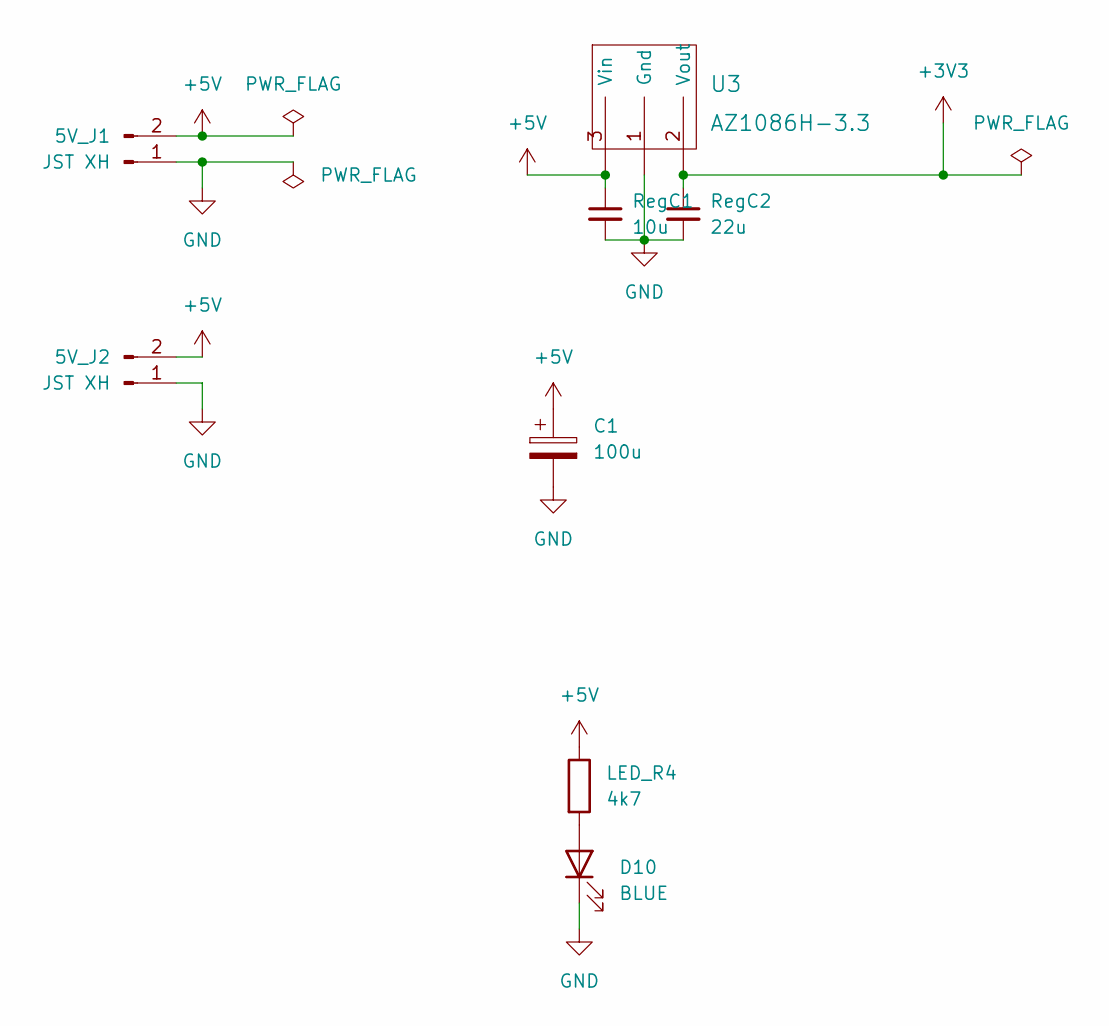
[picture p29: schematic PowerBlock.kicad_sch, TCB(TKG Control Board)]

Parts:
5V_J1, 5V_J2: JST XH; JST_XH_B2B-XH-A_1x02_P2.50mm_Vertical
C1: 100u; CP_Radial_D8.0mm_P5.00mm
D10: BLUE; LED_0603_1608Metric_Pad1.05x0.95mm_HandSolder
LED_R4: 4k7; R_0603_1608Metric_Pad0.98x0.95mm_HandSolder
RegC1: 10u; C_0805_2012Metric_Pad1.18x1.45mm_HandSolder
RegC2: 22u; C_0805_2012Metric_Pad1.18x1.45mm_HandSolder
U3: AZ1086H-3.3; SOT-223-3_TabPin2

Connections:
+3V3: RegC2.1, U3.2 (Vout); also elsewhere on the board
+5V: 5V_J1.2, 5V_J2.2, C1.1, LED_R4.1, RegC1.1, U3.3 (Vin); also elsewhere on the board
GND: 5V_J1.1, 5V_J2.1, C1.2, D10.1 (K), RegC1.2, RegC2.2, U3.1 (Gnd); also elsewhere on the board
unnamed: D10.2 (A), LED_R4.2

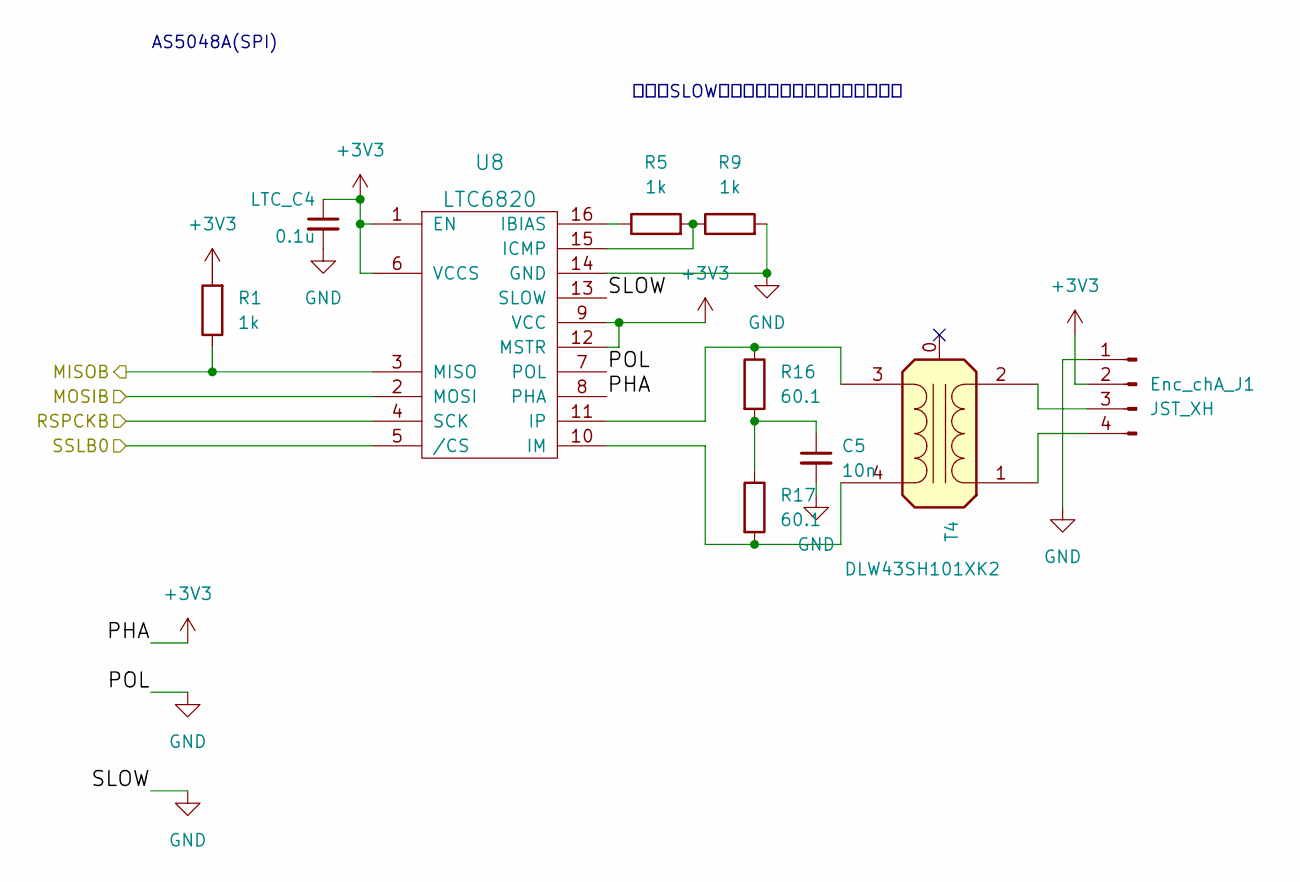
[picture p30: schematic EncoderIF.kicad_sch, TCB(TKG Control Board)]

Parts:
C5: 10n; C_0603_1608Metric_Pad1.08x0.95mm_HandSolder
Enc_chA_J1: JST_XH; JST_XH_B4B-XH-A_1x04_P2.50mm_Vertical
LTC_C4: 0.1u; C_0402_1005Metric_Pad0.74x0.62mm_HandSolder
R1, R5, R9: 1k; R_0603_1608Metric_Pad0.98x0.95mm_HandSolder
R16, R17: 60.1; R_0603_1608Metric_Pad0.98x0.95mm_HandSolder
T4: DLW43SH101XK2
U8: LTC6820; MSOP-16_3x4mm_P0.5mm

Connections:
+3V3: Enc_chA_J1.2, LTC_C4.1, R1.2, U8.1 (EN), U8.6 (VCCS), U8.8 (PHA), U8.9 (VCC), U8.12 (MSTR); also elsewhere on the board
/MISOB: R1.1, U8.3 (MISO); also elsewhere on the board
/MOSIB: U8.2 (MOSI); also elsewhere on the board
/RSPCKB: U8.4 (SCK); also elsewhere on the board
/SSLB0: U8.5 (/CS); also elsewhere on the board
GND: C5.2, Enc_chA_J1.1, LTC_C4.2, R9.2, U8.7 (POL), U8.13 (SLOW), U8.14 (GND); also elsewhere on the board
unnamed: C5.1, R16.2, R17.1
unnamed: Enc_chA_J1.3, T4.2 (AB)
unnamed: Enc_chA_J1.4, T4.1 (AA)
unnamed: R5.1, U8.16 (IBIAS)
unnamed: R5.2, R9.1, U8.15 (ICMP)
unnamed: R16.1, T4.3 (SA), U8.11 (IP)
unnamed: R17.2, T4.4 (SB), U8.10 (IM)

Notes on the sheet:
AS5048A(SPI)
本当にSLOW端子設定はこっちでないとダメ？

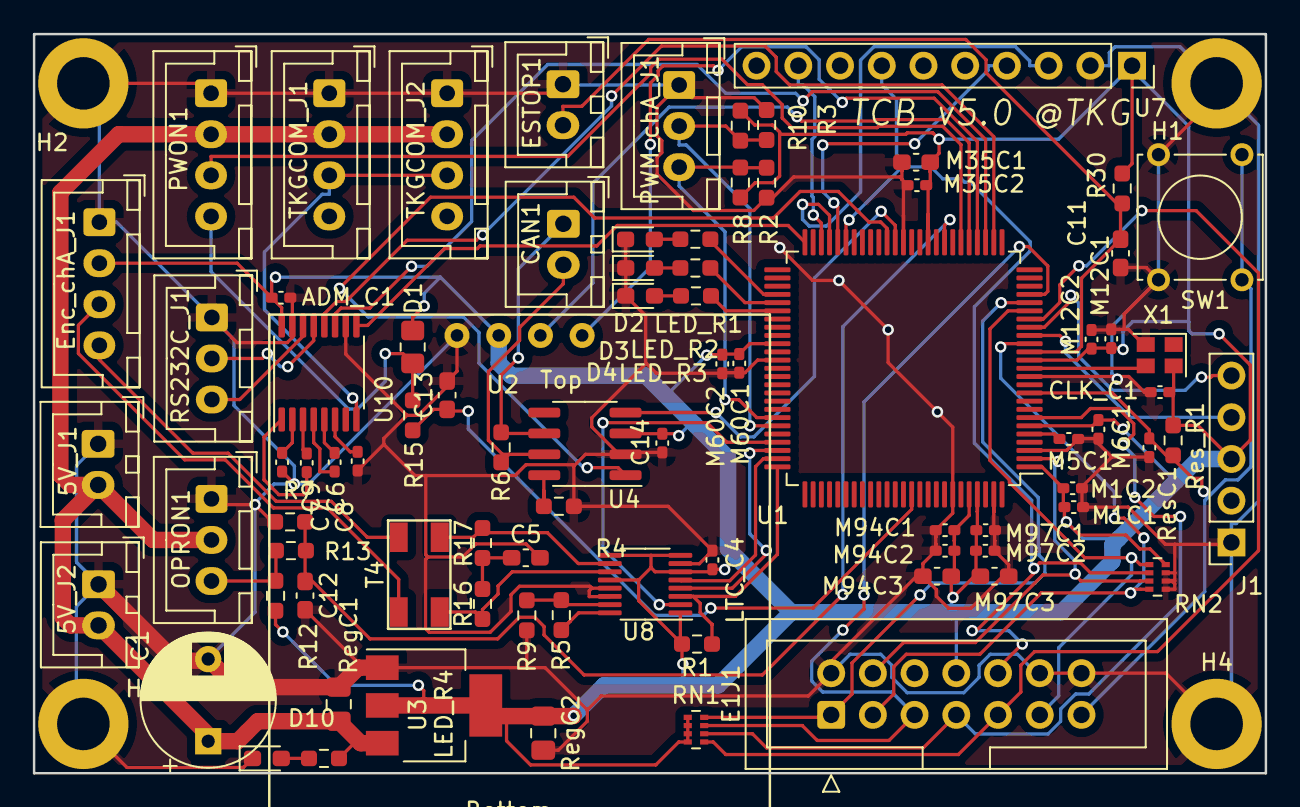
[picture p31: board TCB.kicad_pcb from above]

Board: 2 copper layers, 75.0 x 45.0 mm, 87 parts (0 on the bottom side), 64 nets.

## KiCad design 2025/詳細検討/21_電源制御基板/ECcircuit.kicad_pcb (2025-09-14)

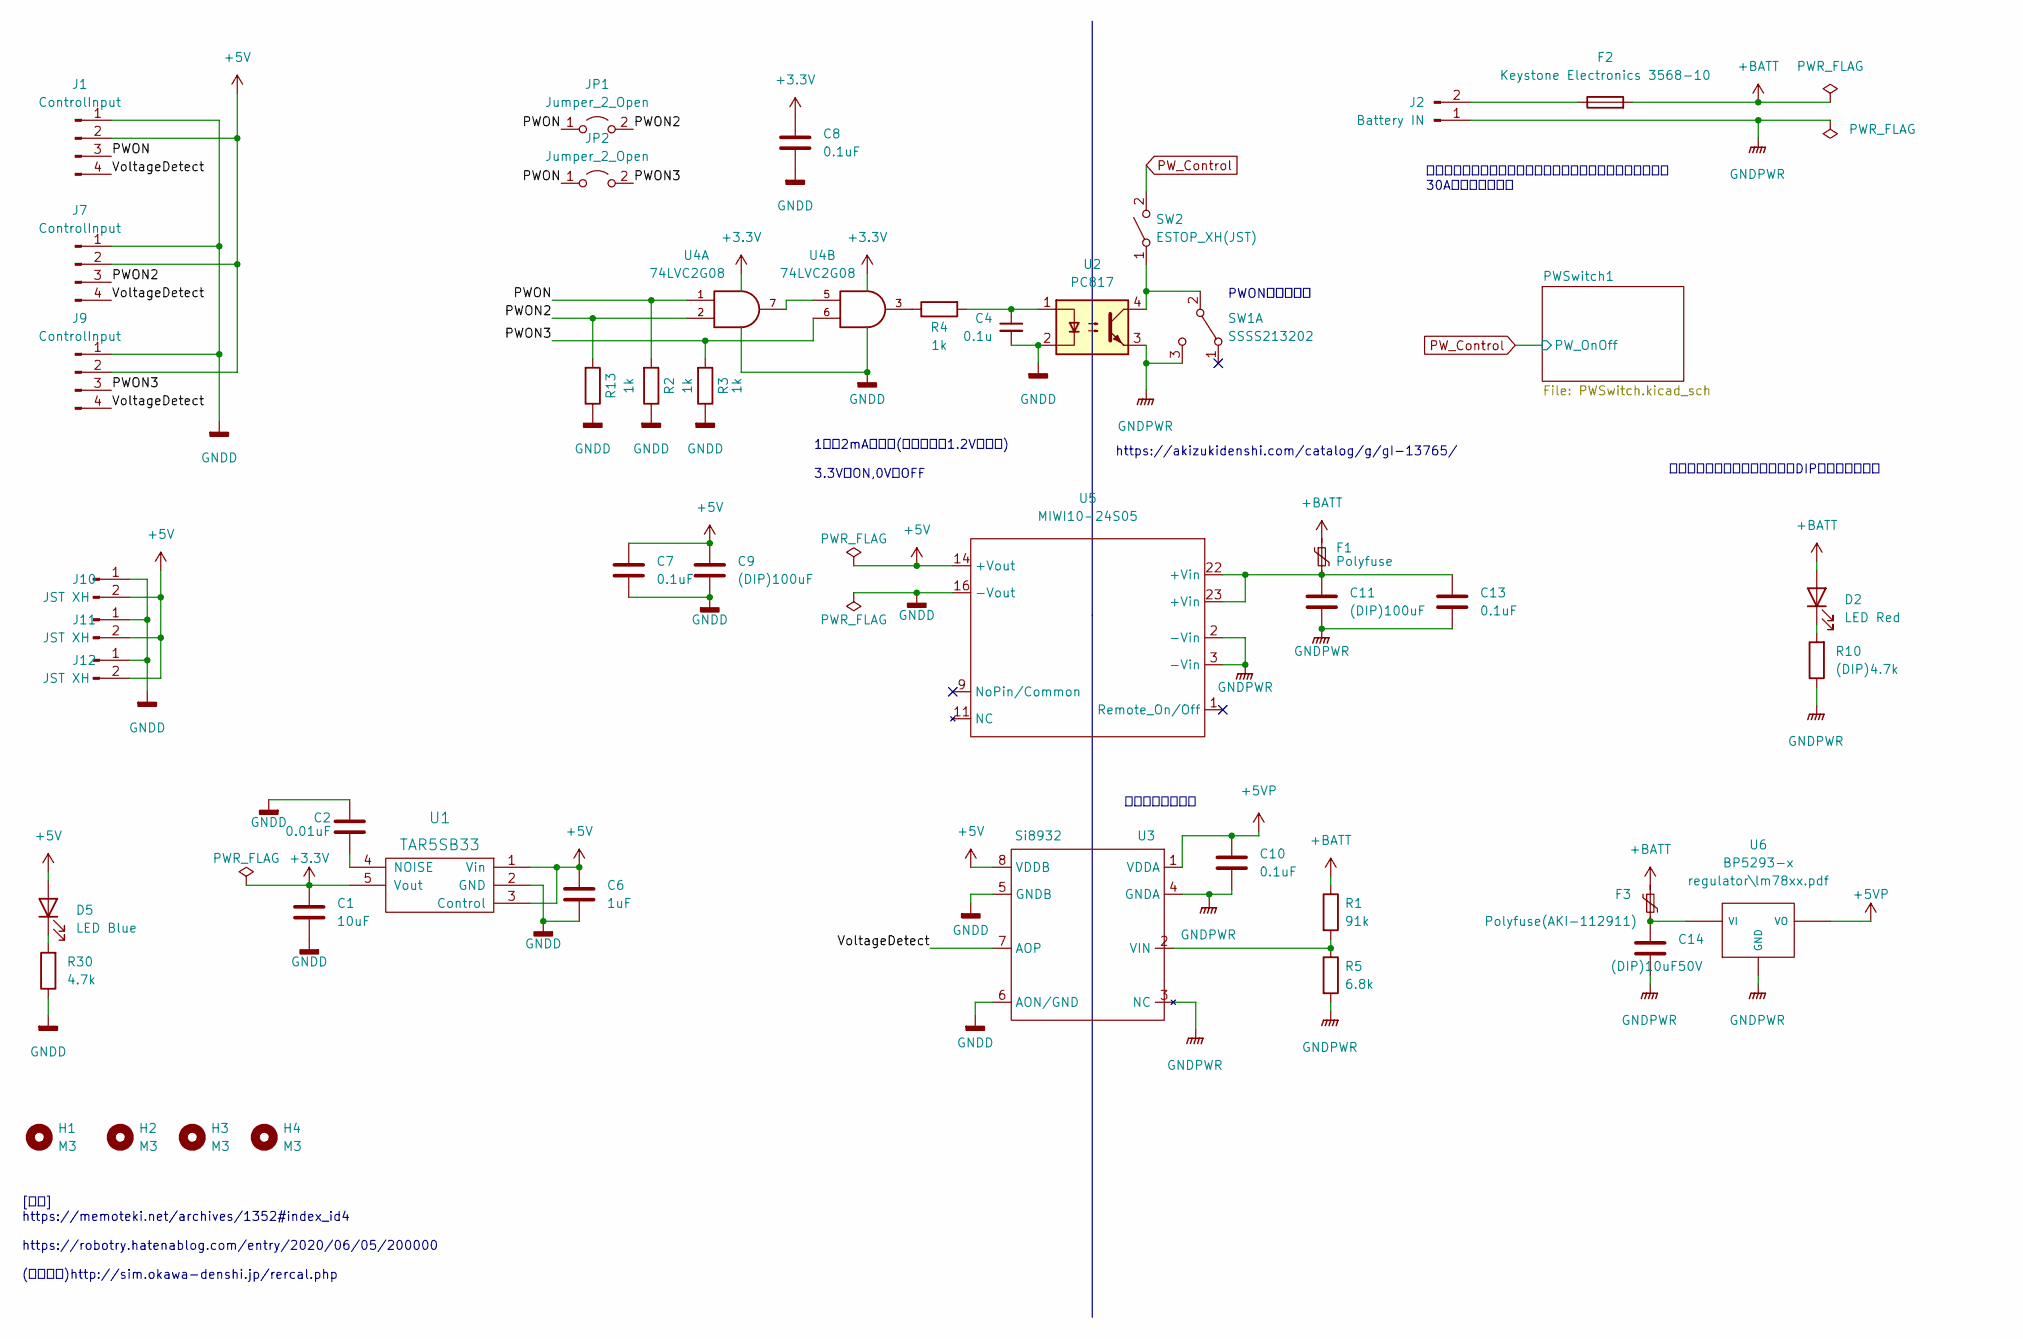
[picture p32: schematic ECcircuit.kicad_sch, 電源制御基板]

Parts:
C1: 10uF; C_0603_1608Metric_Pad1.08x0.95mm_HandSolder
C2: 0.01uF; C_0603_1608Metric_Pad1.08x0.95mm_HandSolder
C4: 0.1u; C_0402_1005Metric_Pad0.74x0.62mm_HandSolder
C6: 1uF; C_0603_1608Metric_Pad1.08x0.95mm_HandSolder
C7, C8, C10, C13: 0.1uF; C_0603_1608Metric_Pad1.08x0.95mm_HandSolder
C9, C11: (DIP)100uF; CP_Radial_D10.0mm_P5.00mm
C14: (DIP)10uF50V; C_Disc_D7.5mm_W2.5mm_P5.00mm
D2: LED Red; D_0603_1608Metric_Pad1.05x0.95mm_HandSolder
D5: LED Blue; D_0603_1608Metric_Pad1.05x0.95mm_HandSolder
F1: Polyfuse; Fuse_Bourns_MF-RG400
F2: Keystone Electronics 3568-10; Fuseholder_Blade_Mini_Keystone_3568
F3: Polyfuse(AKI-112911); Fuse_Bourns_MF-RG400
H1, H2, H3, H4: M3; MountingHole_3.2mm_M3
J1, J7, J9: ControlInput; JST_XH_B4B-XH-A_1x04_P2.50mm_Vertical
J2: Battery IN; AMASS_XT60-M_1x02_P7.20mm_Vertical
J10, J11, J12: JST XH; JST_XH_B2B-XH-A_1x02_P2.50mm_Vertical
JP1, JP2: Jumper_2_Open; PinHeader_1x02_P2.54mm_Vertical
R1: 91k; R_0603_1608Metric_Pad0.98x0.95mm_HandSolder
R2, R3, R4, R13: 1k; R_0603_1608Metric_Pad0.98x0.95mm_HandSolder
R5: 6.8k; R_0603_1608Metric_Pad0.98x0.95mm_HandSolder
R10: (DIP)4.7k; R_Axial_DIN0411_L9.9mm_D3.6mm_P15.24mm_Horizontal
R30: 4.7k; R_0603_1608Metric_Pad0.98x0.95mm_HandSolder
SW1: SSSS213202
SW2: ESTOP_XH(JST); JST_XH_B2B-XH-A_1x02_P2.50mm_Vertical
U1: TAR5SB33; TSOP-5_1.65x3.05mm_P0.95mm
U2: PC817; DIP-4_W7.62mm
U3: Si8932; SOIC-8_3.9x4.9mm_P1.27mm
U4: 74LVC2G08; SSOP-8_2.95x2.8mm_P0.65mm
U5: MIWI10-24S05; DIP-24_W15.24mm
U6: BP5293-x; TO-220-3_Vertical

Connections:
+3.3V: C1.1, C8.1, U1.5 (Vout), U4.8 (VCC)
+5V: C6.1, C7.1, C9.1, D5.2 (A), J1.2, J7.2, J9.2, J10.2, J11.2, J12.2, U1.1 (Vin), U1.3 (Control), U3.8 (VDDB), U5.14 (+Vout)
+5VP: C10.1, U3.1 (VDDA), U6.3 (VO)
+BATT: D2.2 (A), F1.1, F2.2, F3.1, R1.1; also elsewhere on the board
/PWON: J1.3, JP1.1 (A), JP2.1 (A), R2.2, U4.1
/PWON2: J7.3, JP1.2 (B), R13.2, U4.2
/PWON3: J9.3, JP2.2 (B), R3.2, U4.6
/VoltageDetect: J1.4, J7.4, J9.4, U3.7 (AOP)
GND: C1.2, C2.1, C4.2, C6.2, C7.2, C8.2, C9.2, J1.1, J7.1, J9.1, J10.1, J11.1, J12.1, R2.1, R3.1, R13.1, R30.1, U1.2 (GND), U2.2, U3.5 (GNDB), U3.6 (AON/GND), U4.4 (GND), U5.16 (-Vout)
GNDPWR: C10.2, C11.2, C13.2, C14.2, J2.1, R5.2, R10.1, SW1.3 (C), U2.3, U3.3 (NC), U3.4 (GNDA), U5.2 (-Vin), U5.3 (-Vin), U6.2 (GND); also elsewhere on the board
unnamed: C2.2, U1.4 (NOISE)
unnamed: C4.1, R4.2, U2.1
unnamed: C11.1, C13.1, F1.2, U5.22 (+Vin), U5.23 (+Vin)
unnamed: C14.1, F3.2, U6.1 (VI)
unnamed: D2.1 (K), R10.2
unnamed: D5.1 (K), R30.2
unnamed: F2.1, J2.2
unnamed: R1.2, R5.1, U3.2 (VIN)
unnamed: R4.1, U4.3
unnamed: SW1.2 (B), SW2.1 (A), U2.4
unnamed: U4.5, U4.7
PW_Control: SW2.2 (B); also elsewhere on the board

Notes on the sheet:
ヒューズの代わりに電流センサを入れれば、電流計測も可能 30A定格な点に注意
PWON信号無視用
なるべくショート防止のためにDIP部品を使用する
[参考] https://memoteki.net/archives/1352#index_id4 https://robotry.hatenablog.com/entry/2020/06/05/200000 (分圧抵抗)http://sim.okawa-denshi.jp/rercal.php
https://akizukidenshi.com/catalog/g/gI-13765/
1次側2mAとする(順方向電圧1.2Vで計算) 3.3V：ON,0V：OFF
バッテリ電圧検出

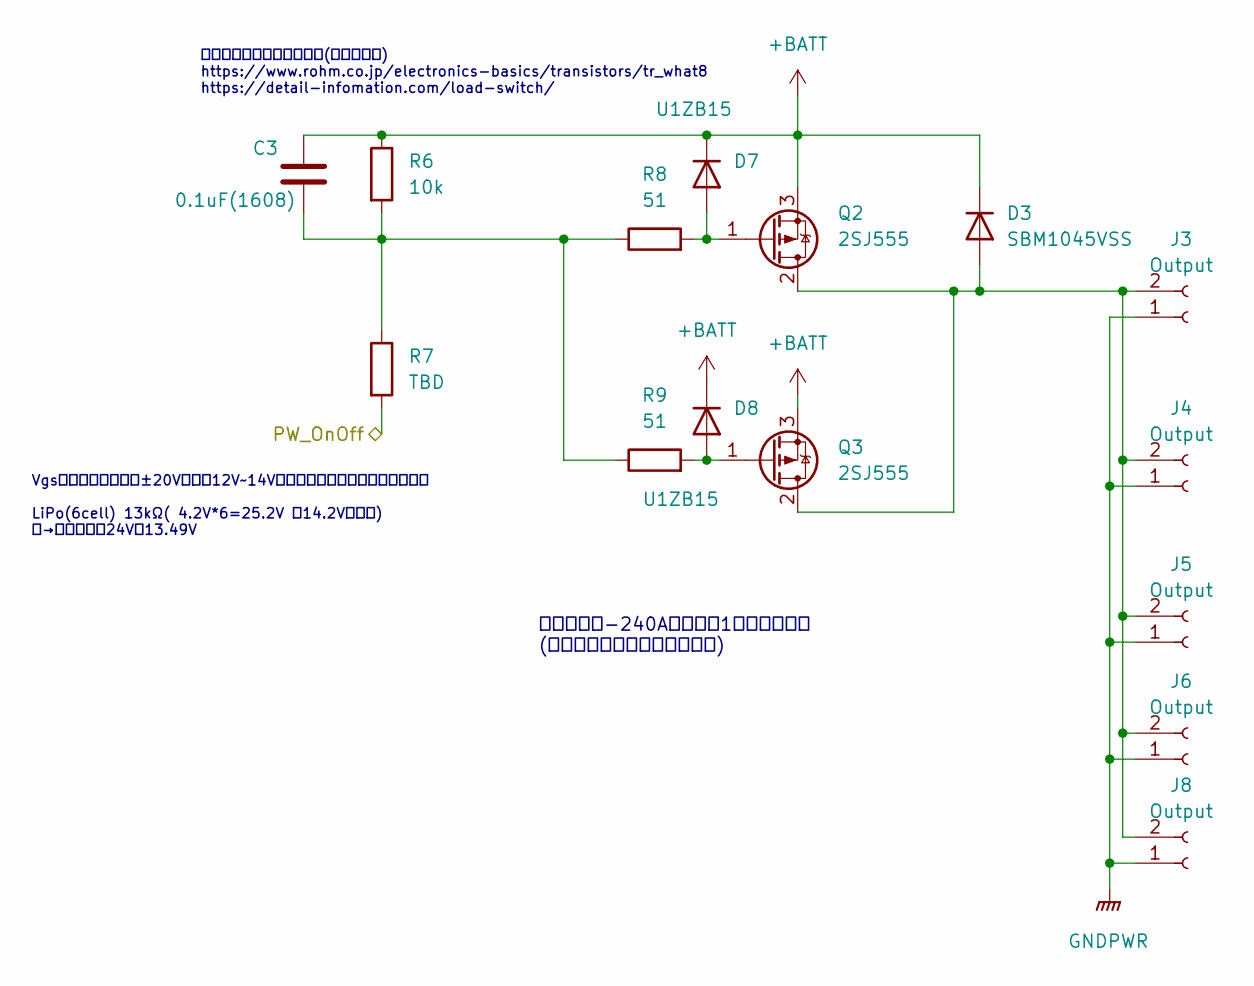
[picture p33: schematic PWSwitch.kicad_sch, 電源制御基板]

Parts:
C3: 0.1uF(1608); C_0603_1608Metric_Pad1.08x0.95mm_HandSolder
D3: SBM1045VSS; D_DO-201_P15.24mm_Horizontal
D7, D8: U1ZB15; D_SMB_Handsoldering
J3, J4: Output; AMASS_XT60-F_1x02_P7.20mm_Vertical
J5, J6, J8: Output; AMASS_XT30U-F_1x02_P5.0mm_Vertical
Q2, Q3: 2SJ555; TO-3P-3_Vertical
R6: 10k; R_0603_1608Metric_Pad0.98x0.95mm_HandSolder
R7: TBD; R_0603_1608Metric_Pad0.98x0.95mm_HandSolder
R8, R9: 51; R_0603_1608Metric_Pad0.98x0.95mm_HandSolder

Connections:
+BATT: C3.1, D3.1 (K), D7.1 (K), D8.1 (K), Q2.3 (S), Q3.3 (S), R6.1; also elsewhere on the board
GNDPWR: J3.1, J4.1, J5.1, J6.1, J8.1; also elsewhere on the board
unnamed: C3.2, R6.2, R7.1, R8.1, R9.1
unnamed: D3.2 (A), J3.2, J4.2, J5.2, J6.2, J8.2, Q2.2 (D), Q3.2 (D)
unnamed: D7.2 (A), Q2.1 (G), R8.2
unnamed: D8.2 (A), Q3.1 (G), R9.2
PW_Control: R7.2; also elsewhere on the board

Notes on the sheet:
突入電流防止用コンデンサ(ソフト充電) https://www.rohm.co.jp/electronics-basics/transistors/tr_what8 https://detail-infomation.com/load-switch/
Vgsの絶対最大定格が±20Vなので12V~14Vとなるような抵抗を選定すること LiPo(6cell) 13kΩ( 4.2V*6=25.2V で14.2Vとなる) →実測結果は24V時13.49V
せん頭電流-240Aのため、1個で問題ない (異常に対する対処はヒューズ)

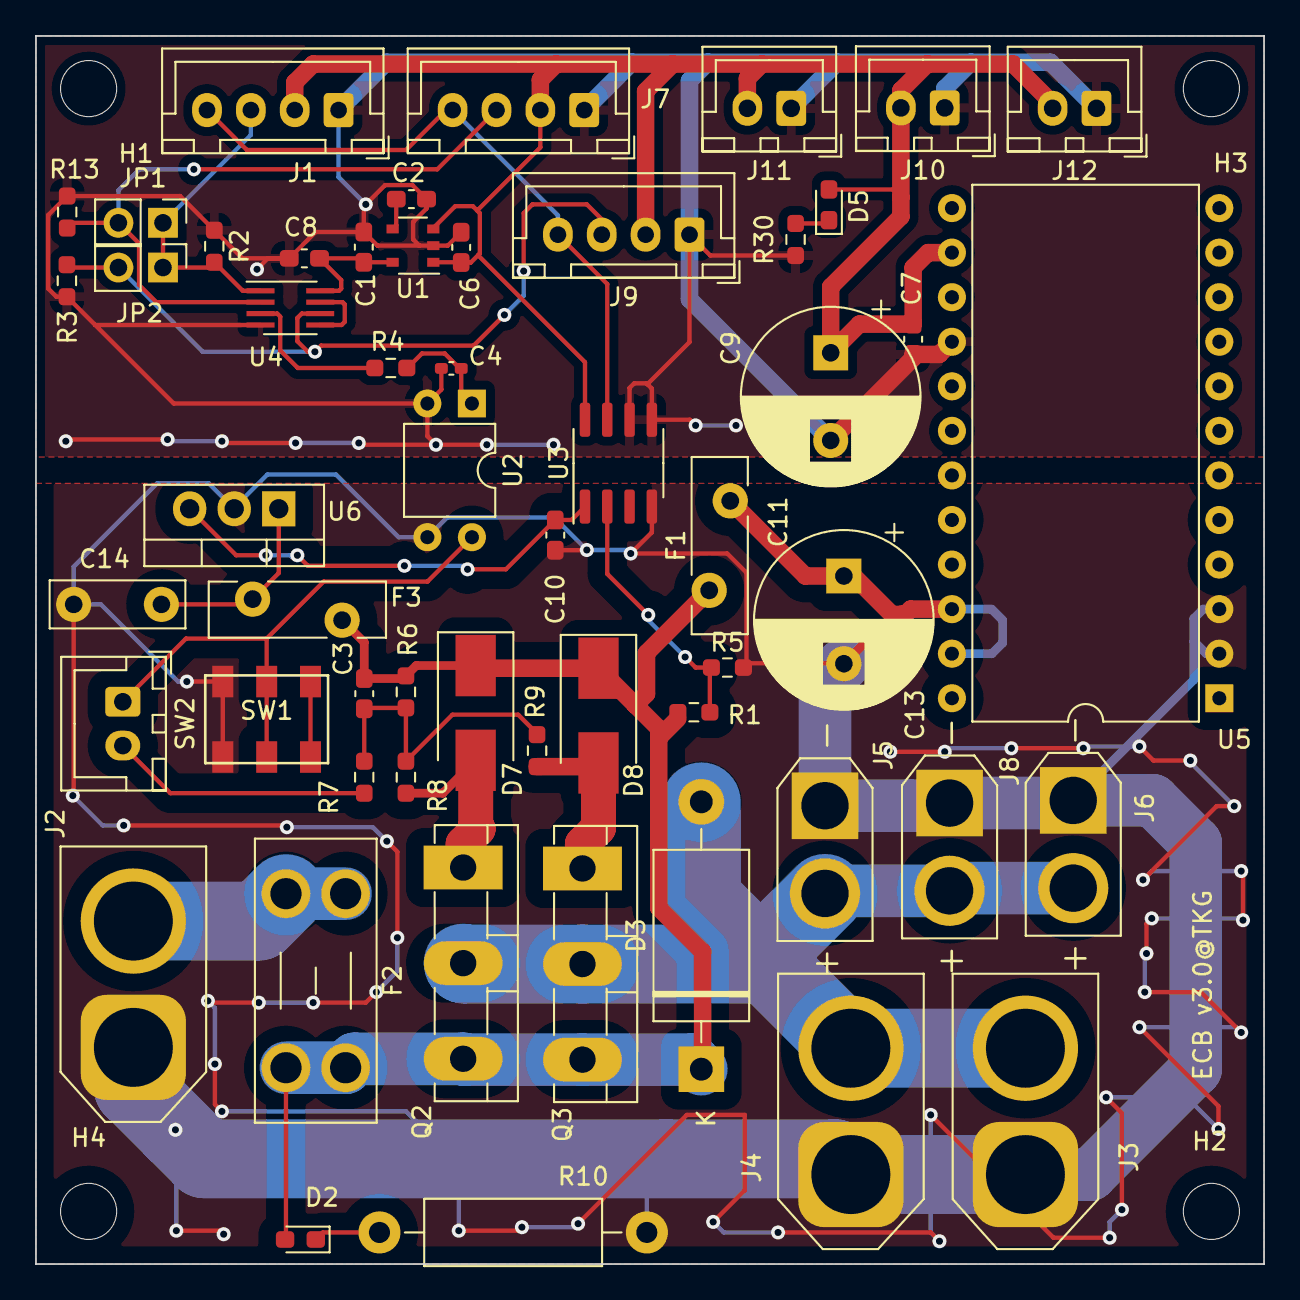
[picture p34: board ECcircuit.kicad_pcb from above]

Board: 2 copper layers, 70.0 x 70.0 mm, 60 parts (0 on the bottom side), 26 nets.

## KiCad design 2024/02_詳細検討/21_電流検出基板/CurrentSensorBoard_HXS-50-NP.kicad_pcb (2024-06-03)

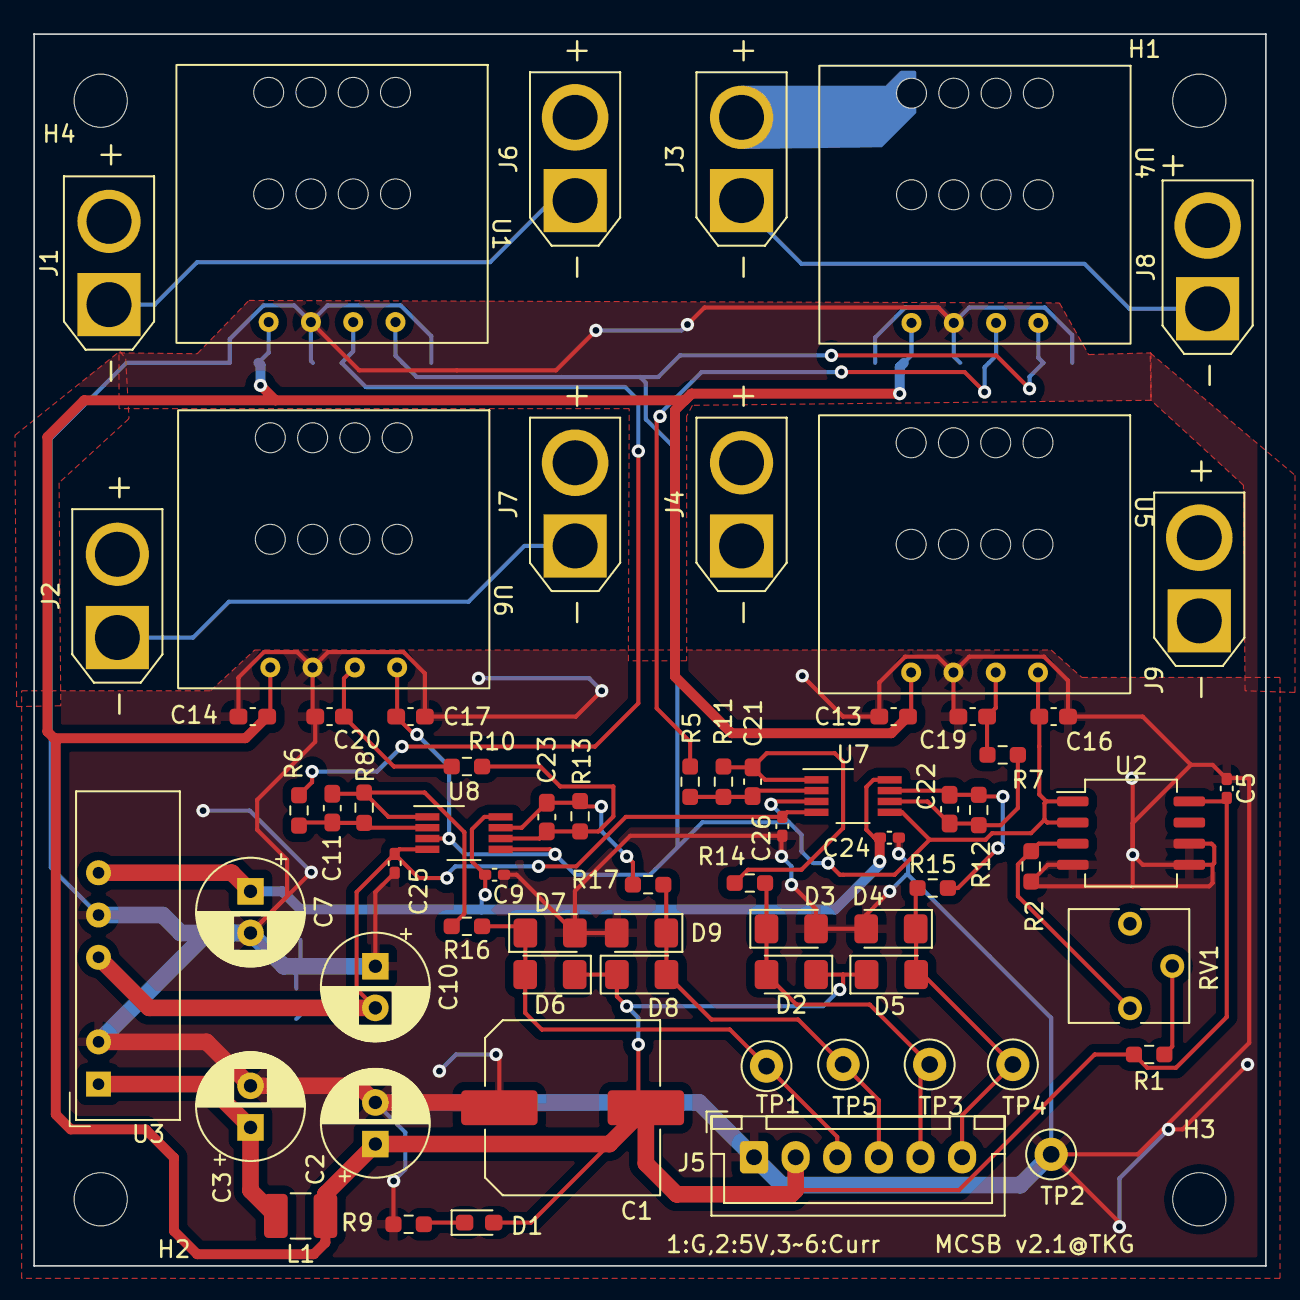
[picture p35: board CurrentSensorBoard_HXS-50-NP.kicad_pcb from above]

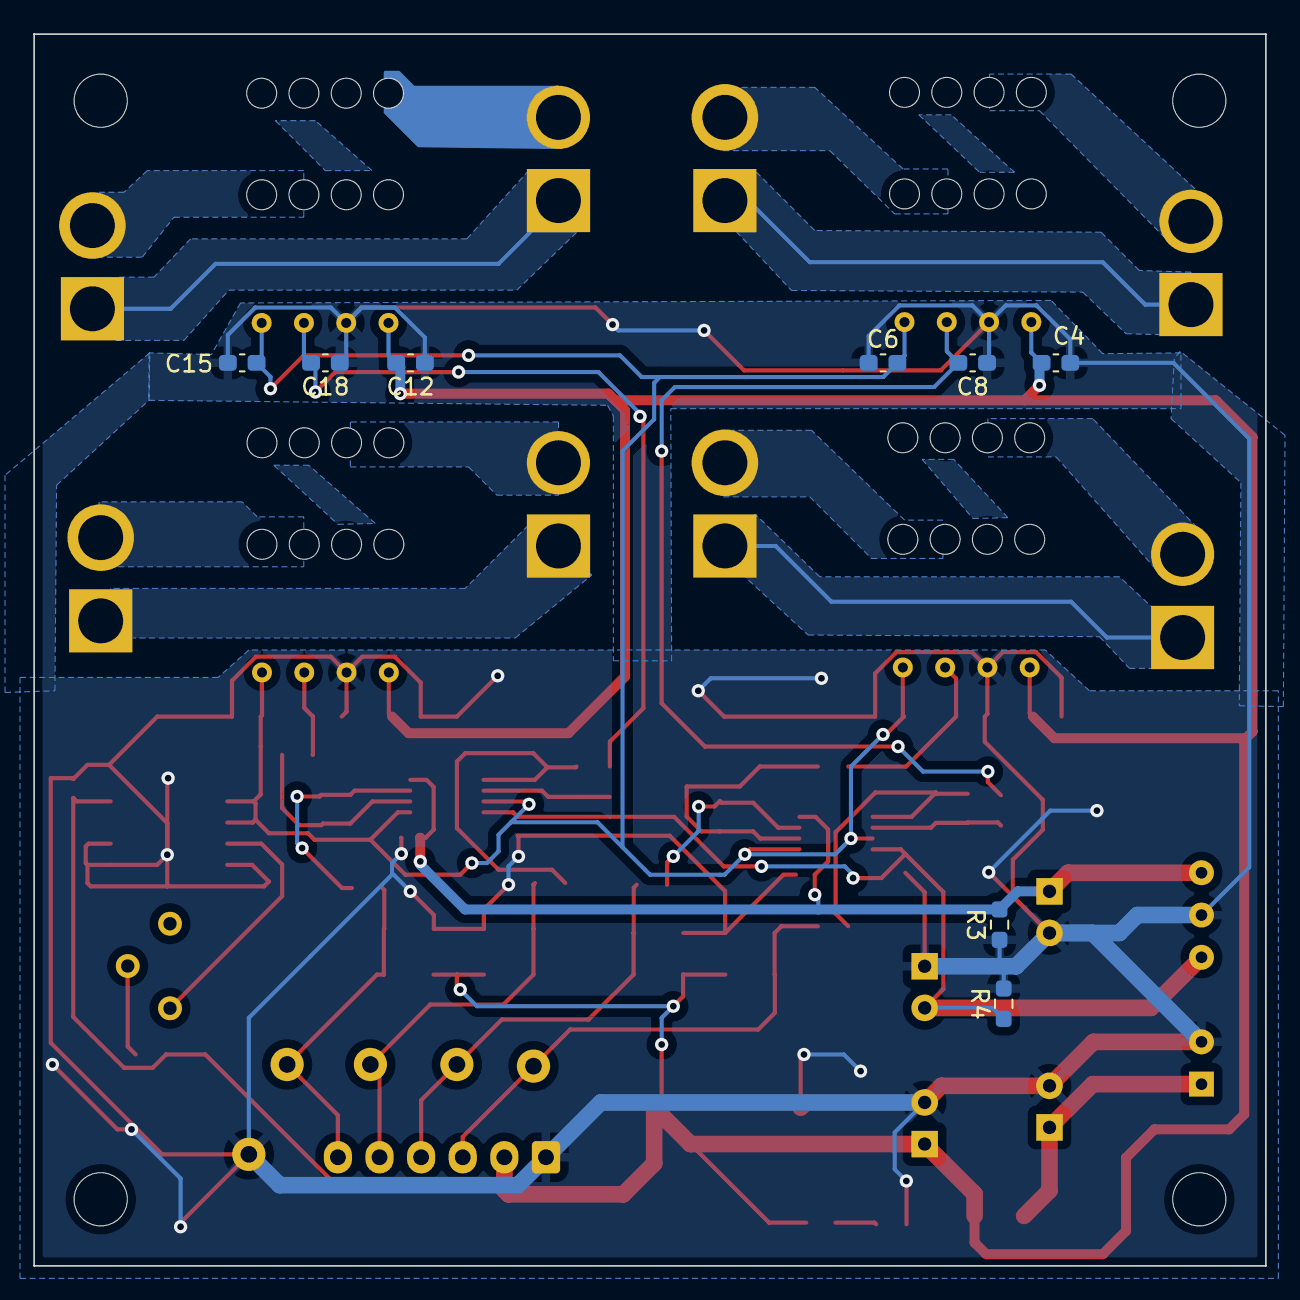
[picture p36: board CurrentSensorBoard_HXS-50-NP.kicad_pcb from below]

Board: 2 copper layers, 74.0 x 74.0 mm, 80 parts (8 on the bottom side), 29 nets.

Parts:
C1: 220uF(P-01302); C_Elec_10x10.2
C2, C3, C7, C10: 22uF(P-08294); CP_Radial_D6.3mm_P2.50mm
C4, C6, C12, C13, C14, C15, C16, C17: 47nF; C_0603_1608Metric_Pad1.08x0.95mm_HandSolder
C5, C24: 0.1uF(NJM2746); C_0402_1005Metric_Pad0.74x0.62mm_HandSolder
C8, C18, C19, C20: 4.7nF; C_0603_1608Metric_Pad1.08x0.95mm_HandSolder
C9, C25, C26: 0.1uF(NJM8502); C_0402_1005Metric_Pad0.74x0.62mm_HandSolder
C11, C21, C22, C23: 0.022uF; C_0603_1608Metric_Pad1.08x0.95mm_HandSolder
D1: BLUE; D_0603_1608Metric_Pad1.05x0.95mm_HandSolder
D2, D3, D4, D5, D6, D7, D8, D9: SS2040FL(I-02073); D_1206_3216Metric_Pad1.42x1.75mm_HandSolder
H1, H2, H3, H4: M3; MountingHole_3.2mm_M3
J1, J2, J3, J4: XT30; AMASS_XT30U-M_1x02_P5.0mm_Vertical
J5: JST XH; JST_XH_B6B-XH-A_1x06_P2.50mm_Vertical
J6, J7, J8, J9: XT30; AMASS_XT30U-F_1x02_P5.0mm_Vertical
L1: 4.7uH(P-14978); L_1210_3225Metric_Pad1.42x2.65mm_HandSolder
R1: 100k; R_0603_1608Metric_Pad0.98x0.95mm_HandSolder
R2: 51k; R_0603_1608Metric_Pad0.98x0.95mm_HandSolder
R3, R4, R5, R6, R7, R10: 10k; R_0603_1608Metric_Pad0.98x0.95mm_HandSolder
R8, R11, R12, R13: 27k; R_0603_1608Metric_Pad0.98x0.95mm_HandSolder
R9: 4.7k; R_0603_1608Metric_Pad0.98x0.95mm_HandSolder
R14, R15, R16, R17: 1k; R_0603_1608Metric_Pad0.98x0.95mm_HandSolder
RV1: 10k(P-03277); Potentiometer_Vishay_T73YP_Vertical
TP1, TP3, TP4, TP5: Curr; TestPoint_Loop_D1.80mm_Drill1.0mm_Beaded
TP2: Gnd; TestPoint_Loop_D1.80mm_Drill1.0mm_Beaded
U1, U4, U5, U6: HXS_50-NP; HXS_50-NP-NoPad
U2: NJM2746; SO-8_5.3x6.2mm_P1.27mm
U3: MAU108; Converter_DCDC_Murata_NMAxxxxSC_THT
U7, U8: NJM8502; VSSOP-8_3.0x3.0mm_P0.65mm

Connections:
+5V: C1.2, C2.1, C4.2, C5.2, C12.2, C13.2, C14.2, D1.2 (A), D2.1 (K), D4.1 (K), D6.1 (K), D8.1 (K), J5.2, L1.1, R1.2, U1.9 (Vcc), U2.8 (V+), U4.9 (Vcc), U5.9 (Vcc), U6.9 (Vcc)
+12V: C7.1, C9.2, C24.2, R3.2, U3.6 (VOUT+), U7.8 (V+), U8.8 (V+)
-12V: C10.2, C25.2, C26.2, R4.1, U3.4 (VOUT-), U7.4 (V-), U8.4 (V-)
Cur1: D6.2 (A), D7.1 (K), J5.3, R16.1, TP1.1
Cur2: D8.2 (A), D9.1 (K), J5.4, R17.1, TP5.1
Cur3: D2.2 (A), D3.1 (K), J5.5, R14.1, TP3.1
Cur4: D4.2 (A), D5.1 (K), J5.6, R15.1, TP4.1
GND: C1.1, C2.2, C3.2, C4.1, C5.1, C6.1, C7.2, C8.1, C9.1, C10.1, C12.1, C13.1, C14.1, C15.1, C16.1, C17.1, C18.1, C19.1, C20.1, C24.1, C25.1, C26.1, D3.2 (A), D5.2 (A), D7.2 (A), D9.2 (A), J5.1, R2.1, R3.1, R4.2, R9.1, TP2.1, U1.10 (Gnd), U2.4 (V-), U2.5 (+), U2.6 (-), U3.2 (VIN-), U3.5 (0V), U4.10 (Gnd), U5.10 (Gnd), U6.10 (Gnd)
unnamed: C3.1, L1.2, U3.1 (VIN+)
unnamed: C8.2, R6.1, U1.11 (Out)
unnamed: C11.1, R6.2, R8.1, U8.2 (-)
unnamed: C11.2, R8.2, R16.2, U8.1
unnamed: C18.2, R5.1, U4.11 (Out)
unnamed: C19.2, R7.1, U5.11 (Out)
unnamed: C20.2, R10.1, U6.11 (Out)
unnamed: C21.1, R5.2, R11.1, U7.2 (-)
unnamed: C21.2, R11.2, R14.2, U7.1
unnamed: C22.1, R7.2, R12.1, U7.6 (-)
unnamed: C22.2, R12.2, R15.2, U7.7
unnamed: C23.1, R10.2, R13.1, U8.6 (-)
unnamed: C23.2, R13.2, R17.2, U8.7
unnamed: D1.1 (K), R9.2
unnamed: J1.1, J6.1
unnamed: J2.1, J7.1
unnamed: J3.1, J8.1
unnamed: J4.1, J9.1
unnamed: R1.1, RV1.2
unnamed: R2.2, RV1.1, U2.3 (+)
ref1.65V: C6.2, C15.2, C16.2, C17.2, U1.12 (Ref), U2.1, U2.2 (-), U4.12 (Ref), U5.12 (Ref), U6.12 (Ref), U7.3 (+), U7.5 (+), U8.3 (+), U8.5 (+)

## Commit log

2024-06-03 add 2024
    [CH1.kicad_sch, CoREリスクアセスメントシート_TKG.xlsx, CurrentSensorBoard_HXS-50-NP.kicad_pcb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]
2025-02-16 [add] READMEを追加
2025-02-16 [change] STEPファイルのZIP圧縮版を詳細検討フォルダに移動
2025-09-14 upgrade 2025年度資料追加
    [CH1.kicad_sch, CoREリスクアセスメントシート_TKG.xlsx, DataTransfer.kicad_sch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]
2025-09-14 Rename 01-4_詳細設計レビュー(2024-2025)_v0.7.pdf to 01-4-1_詳細設計レビュー(2024-2025)_v0.7.pdf
    ファイル名修正
2025-09-14 1-4-1_詳細設計レビュー(2024-2025)_v0.7を削除
2025-09-14 詳細設計検討書を再アップロード
